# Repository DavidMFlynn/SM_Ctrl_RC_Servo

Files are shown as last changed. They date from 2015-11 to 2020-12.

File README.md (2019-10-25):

# SM_Ctrl_RC_Servo
Model railroad switch machine controller.
Uses a small (SG90) R/C Servo as a switch machine.
Built for the Highland Pacific, 854 East Broadway, San Gabriel, CA 91776, USA
GPL 3+
If you find it useful let me know dflynn at oxfordvue.com
The G2R Rev B may be the final version. A remote config connector and a big capacitor were added.
My faverite servo is the hobbyking HX5010 it's inexpensive and well behaved.

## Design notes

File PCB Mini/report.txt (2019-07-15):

Info: Backing up file “/Projects/SM_Ctrl_RC_Servo/PCB Mini/sym-lib-table” to file “/Projects/SM_Ctrl_RC_Servo/PCB Mini/rescue-backup/sym-lib-table-2019-07-13-21-21-59”.
Info: Backing up file “/Projects/SM_Ctrl_RC_Servo/PCB Mini/RCSMCtrl.sch” to file “/Projects/SM_Ctrl_RC_Servo/PCB Mini/rescue-backup/RCSMCtrl-2019-07-13-21-21-59.sch”.
Info: Backing up file “/Projects/SM_Ctrl_RC_Servo/PCB Mini/RCSMCtrl.pro” to file “/Projects/SM_Ctrl_RC_Servo/PCB Mini/rescue-backup/RCSMCtrl-2019-07-13-21-21-59.pro”.
Info: Backing up file “/Projects/SM_Ctrl_RC_Servo/PCB Mini/RCSMCtrl-cache.lib” to file “/Projects/SM_Ctrl_RC_Servo/PCB Mini/rescue-backup/RCSMCtrl-cache-2019-07-13-21-21-59.lib”.
Info: Backing up file “/Projects/SM_Ctrl_RC_Servo/PCB Mini/RCSMCtrl-rescue.lib” to file “/Projects/SM_Ctrl_RC_Servo/PCB Mini/rescue-backup/RCSMCtrl-rescue-2019-07-13-21-21-59.lib”.
Info: Backing up file “/Projects/SM_Ctrl_RC_Servo/PCB Mini/RCSMCtrl-rescue.dcm” to file “/Projects/SM_Ctrl_RC_Servo/PCB Mini/rescue-backup/RCSMCtrl-rescue-2019-07-13-21-21-59.dcm”.
Info: Adding library “RCSMCtrl-rescue”, file “${KIPRJMOD}/RCSMCtrl-rescue.lib” to project symbol library table.
Symbol “PIC12(L)F1822-I_P” mapped to symbol library “RCSMCtrl-rescue”.
Symbol “D” mapped to symbol library “Device”.
Symbol “CP1_Small” mapped to symbol library “Device”.
Symbol “C_Small” mapped to symbol library “Device”.
Symbol “C_Small” mapped to symbol library “Device”.
Symbol “LM7805CT” mapped to symbol library “RCSMCtrl-rescue”.
Symbol “CONN_01X15” mapped to symbol library “RCSMCtrl-rescue”.
Symbol “+5V” mapped to symbol library “power”.
Symbol “GND” mapped to symbol library “power”.
Symbol “+24V” mapped to symbol library “power”.
Symbol “GND” mapped to symbol library “power”.
Symbol “CONN_01X03” mapped to symbol library “RCSMCtrl-rescue”.
Symbol “+5V” mapped to symbol library “power”.
Symbol “GND” mapped to symbol library “power”.
Symbol “R” mapped to symbol library “Device”.
Symbol “+5V” mapped to symbol library “power”.
Symbol “GND” mapped to symbol library “power”.
Symbol “R” mapped to symbol library “Device”.
Symbol “D” mapped to symbol library “Device”.
Symbol “R” mapped to symbol library “Device”.
Symbol “R” mapped to symbol library “Device”.
Symbol “C_Small” mapped to symbol library “Device”.
Symbol “Q_NPN_EBC” mapped to symbol library “Device”.
Symbol “Q_PNP_EBC” mapped to symbol library “Device”.
Symbol “R” mapped to symbol library “Device”.
Symbol “GND” mapped to symbol library “power”.
Symbol “+5V” mapped to symbol library “power”.
Symbol “GND” mapped to symbol library “power”.
Symbol “SW_PUSH” mapped to symbol library “RCSMCtrl-rescue”.
Symbol “SW_PUSH” mapped to symbol library “RCSMCtrl-rescue”.
Symbol “LED” mapped to symbol library “Device”.
Symbol “LED” mapped to symbol library “Device”.
Symbol “+5V” mapped to symbol library “power”.
Symbol “R” mapped to symbol library “Device”.
Symbol “R” mapped to symbol library “Device”.
Symbol “R” mapped to symbol library “Device”.
Symbol “R” mapped to symbol library “Device”.
Symbol “GND” mapped to symbol library “power”.
Symbol “D” mapped to symbol library “Device”.
Symbol “D” mapped to symbol library “Device”.
Symbol “GND” mapped to symbol library “power”.
Symbol “+24V” mapped to symbol library “power”.
Symbol “R” mapped to symbol library “Device”.
Symbol “R” mapped to symbol library “Device”.
Symbol “Q_NPN_EBC” mapped to symbol library “Device”.
Symbol “D” mapped to symbol library “Device”.
Symbol “D” mapped to symbol library “Device”.
Symbol “GND” mapped to symbol library “power”.
Symbol “+24V” mapped to symbol library “power”.
Symbol “R” mapped to symbol library “Device”.
Symbol “R” mapped to symbol library “Device”.
Symbol “IM00” mapped to symbol library “RCSMCtrl-rescue”.
Symbol “IM00” mapped to symbol library “RCSMCtrl-rescue”.
Info: Symbol library table mapping complete!

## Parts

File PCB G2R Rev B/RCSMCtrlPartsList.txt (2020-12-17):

R/C Servo Sitch Machine Controller Parts List
=========================================================
P1	Wires 15 x 10" 20AWG
P2	Connector 3 pin .1cl

K1,K2	Relay G2R 24VDC DPDT (1 or 2)

U1	LM7805 DPAK
IC1	Socket 8 pin dip (optional)
IC1	PIC12F1822

Q1,Q3	2N7000 40V N-Ch FET TO-92 (2)
Q2	2N3906 40V PNP TO-92

D1,D2,D3,D4,D7,D8	Diode 200V Fast SMA (6)
D5,D6	LED 1206 (2)
SW1,SW1	Switch SMT SPST

C1,C3,C4,C6	Cap 0.1uf 0805 (3)
C2	Cap 33uf 50v
C5                     Cap 220uf 16v

R1,R5,R6,R7,R9,R12	Res 47KΩ 0805 (6)
R2,R3,R8,R10,R13	Res 1KΩ 0805 (5)
R4	Res 10KΩ 0805
R11	Res 220Ω 0805

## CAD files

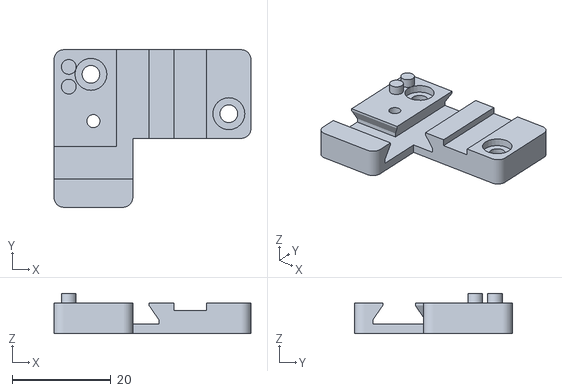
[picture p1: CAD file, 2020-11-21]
MountingBox/AtlasTurnout STL/RAMountingBlock.stl
40.0 x 32.0 x 8.15

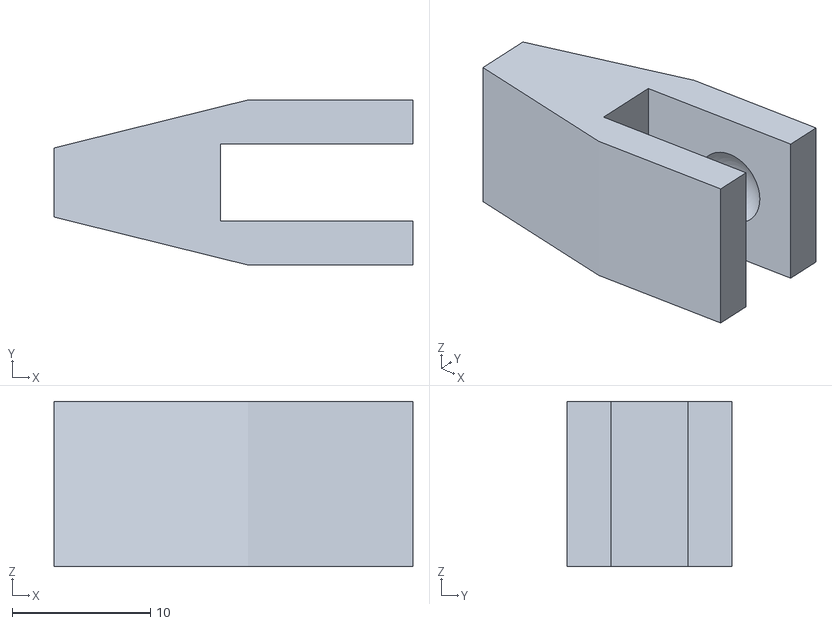
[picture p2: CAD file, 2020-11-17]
MountingBox/STL/RodConnector.stl
26.0 x 11.9 x 11.9

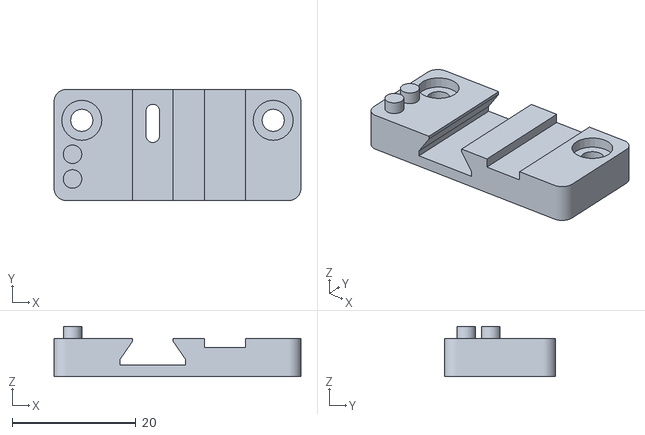
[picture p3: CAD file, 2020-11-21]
MountingBox/AtlasTurnout STL/MountingBlockMir.stl
40.0 x 18.0 x 8.15

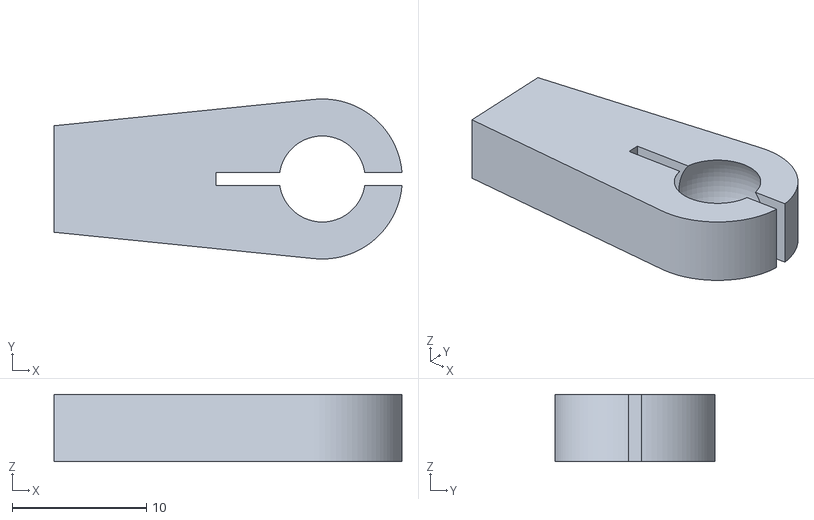
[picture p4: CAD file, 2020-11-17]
MountingBox/STL/RodEnd.stl
25.9 x 11.9 x 5.00

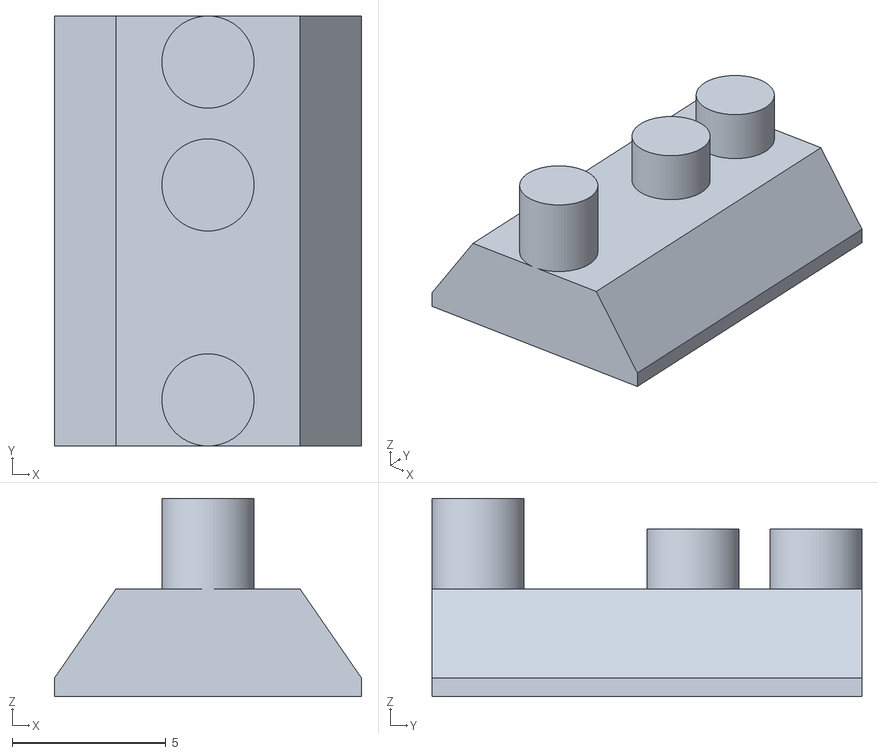
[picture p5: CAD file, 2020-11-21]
MountingBox/AtlasTurnout STL/RASlider.stl
10.0 x 14.0 x 6.45

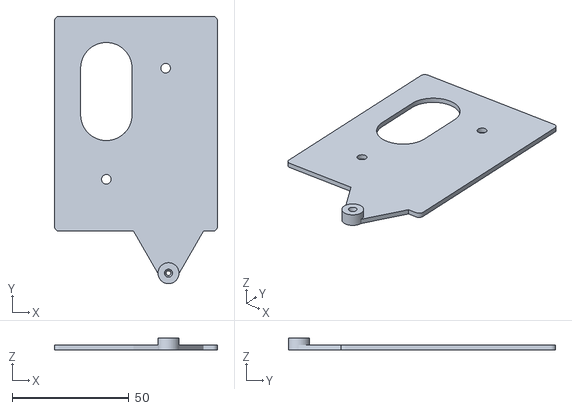
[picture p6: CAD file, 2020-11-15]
MountingBox/STL/PivotBaseR.stl
69.8 x 114.6 x 5.00

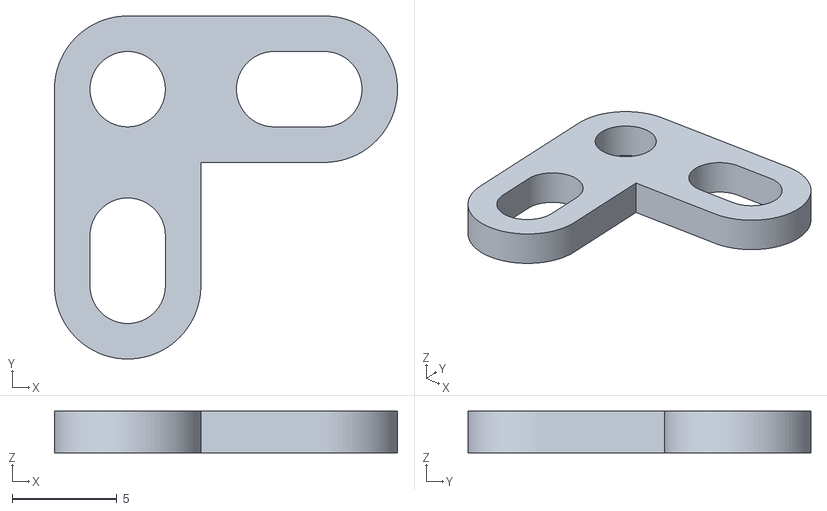
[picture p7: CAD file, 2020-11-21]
MountingBox/AtlasTurnout STL/RAPivot.stl
16.4 x 16.4 x 2.00

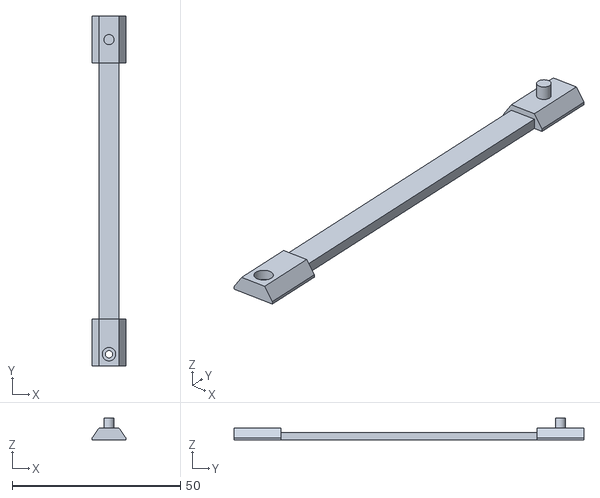
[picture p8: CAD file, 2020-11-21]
MountingBox/AtlasTurnout STL/RAExtension90.stl
10.0 x 104.0 x 6.45

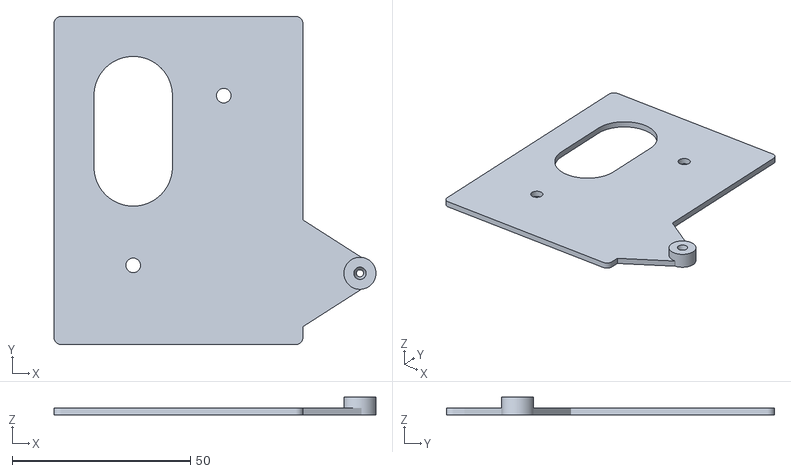
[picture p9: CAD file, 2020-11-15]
MountingBox/STL/PivotBaseRS.stl
90.3 x 92.1 x 5.00

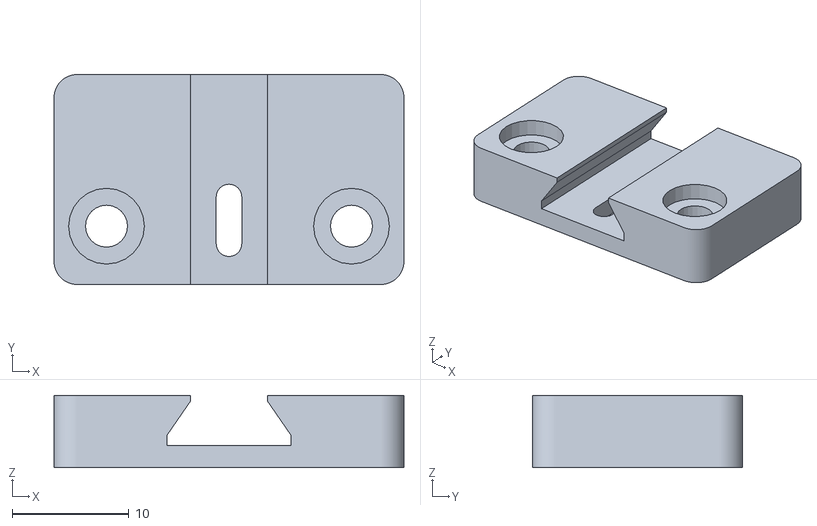
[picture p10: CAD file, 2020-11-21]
MountingBox/AtlasTurnout STL/ExtenderMount.stl
30.0 x 18.0 x 6.20

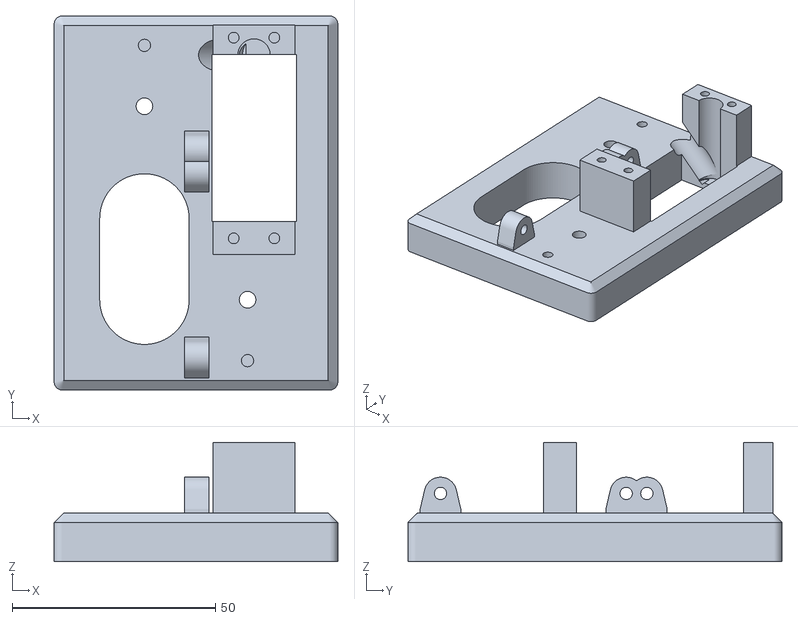
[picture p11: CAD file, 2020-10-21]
MountingBox/STL/ServoSMBlockHX5010.stl
69.8 x 92.1 x 29.3

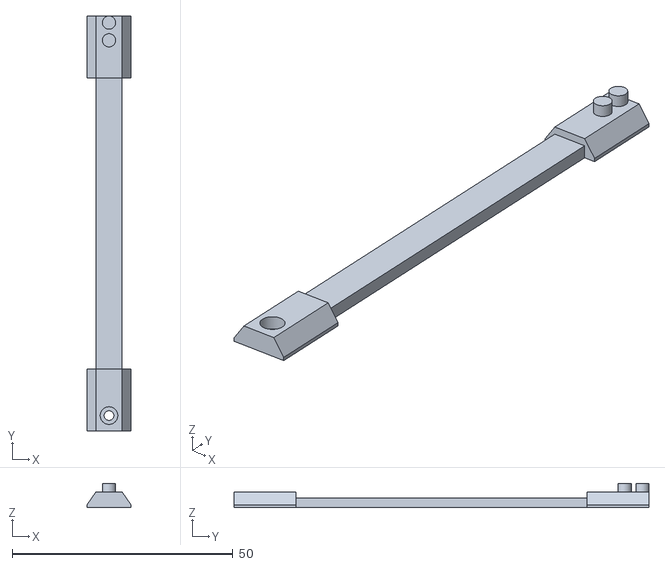
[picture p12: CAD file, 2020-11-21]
MountingBox/AtlasTurnout STL/ExtendedSlider80.stl
10.0 x 94.0 x 5.45

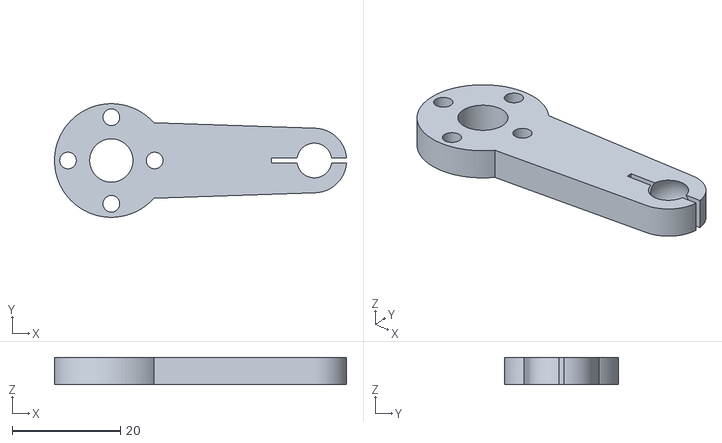
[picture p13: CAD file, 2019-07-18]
MountingBox/STL/ServoArmMG996R.stl
53.9 x 21.0 x 5.00

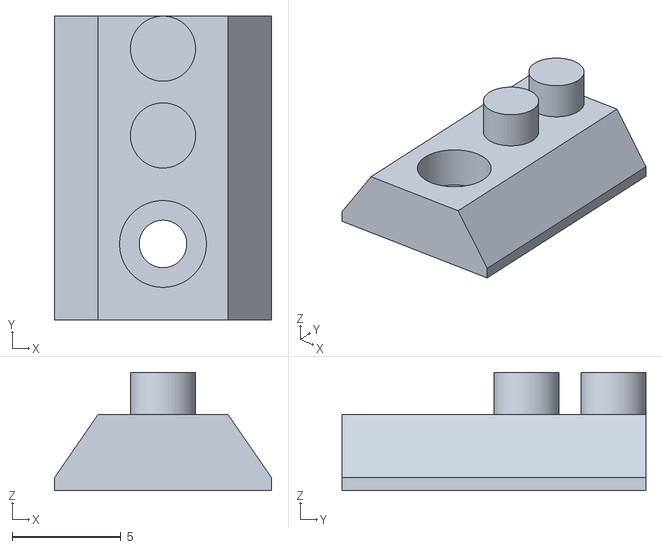
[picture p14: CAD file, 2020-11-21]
MountingBox/AtlasTurnout STL/Slider.stl
10.0 x 14.0 x 5.45

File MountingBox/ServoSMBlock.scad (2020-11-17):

// *************************************************
// Standard Servo Switch Machine Block & Adaptor
// by Dave Flynn
// Filename:ServoSMBlock.scad
// Created: 8/18/2018
// Revision: 1.2 11/16/2020
// Units: mm
// **************************************************
//  ***** History ******
// 1.2 11/16/2020 Added extension arm parts
// 1.1 10/26/2020 Added PivotBase
// 1.0b1 8/6/2019 Added #6 screw hole for wire strain relief.
// 1.0a2 8/4/2019 Common mounting for PCB.
// 1.0a1 7/17/2019 RC1, Servo and PCB mount, Ball servo horn.
// 1.0d1 8/18/2018 First rev'd version
//
// **************************************************
//  ***** for STL output *****
// Arm(L=37.5);
//
// RodEnd(L=20); // part of extension arm
// rotate([90,0,0]) RodConnector(L=20); // part of extension arm
//
// SMBlock(PCBMount="Both");
// mirror([1,0,0]) SMBlock(PCBMount="Both"); // Left side mount
// SMBlock(PCBMount="G2RrA");
// mirror([1,0,0]) SMBlock(PCBMount="G2RrA"); // Left side mount
//
// rotate([180,0,0]) PivotBase(); // for right mount
// rotate([180,0,0]) mirror([1,0,0]) PivotBase(); // for left mount
// rotate([180,0,0]) PivotBaseSide(); // for right side mount
// rotate([180,0,0]) mirror([1,0,0]) PivotBaseSide(); // for left side mount
//
// **************************************************


include<CommonStuffSAEmm.scad>
include<LD-20MGServoLib.scad>

$fn=90;
Overlap=0.05;
IDXtra=0.2;

module RodConnector(L=20){
	Ball_d=5/16*25.4;
	Arm_h=5;
	
	difference(){
		hull(){
			translate([0,-Ball_d/2-2,-Arm_h/2]) cube([0.1,Ball_d+4,Arm_h]);
			
			translate([L,0,0]) //cylinder(d=Ball_d+4,h=Ball_d+4,center=true);
			cube([Ball_d+4,Ball_d+4,Ball_d+4],center=true);
		} // hull
		
		
		//Mounting Rod
		translate([0,0,0]) rotate([0,-90,0]) Bolt6Hole(depth=10);
		
		// the ball
		translate([L,0,0]) sphere(d=Ball_d+IDXtra,$fn=60);
		translate([L,0,0]) cube([Ball_d+8,Ball_d+7,Arm_h+IDXtra*3],center=true); //cylinder(d=Ball_d+7,h=Arm_h+IDXtra*3,center=true);
		
		
	} // difference
} // RodConnector

//RodConnector();

module RodEnd(L=20){
	Ball_d=5/16*25.4;
	Arm_h=5;
	
	difference(){
			
		hull(){
			translate([0,-Ball_d/2,0]) cube([0.1,Ball_d,Arm_h]);
			translate([L,0,0]) cylinder(d=Ball_d+4,h=Arm_h);
		} // hull
			
		//Mounting Rod
		translate([0,0,Arm_h/2]) rotate([0,-90,0]) Bolt6Hole(depth=10);
		// the ball
		translate([L,0,Arm_h/2]) sphere(d=Ball_d+IDXtra,$fn=60);
		//translate([L,0,-Overlap]) cylinder(d=Ball_d*0.707,h=Arm_h+Overlap*2);
		
		// slot
		translate([L-Ball_d,-0.5,-Overlap]) cube([Ball_d*2+Overlap,1,Arm_h+Overlap*2]);
		
	} // diff
	
} // RodEnd

//RodEnd();

module Arm(L=37.5){
	// Arm for MG996R servo
	//Ball_d=3/8*25.4;
	Ball_d=5/16*25.4;
	Arm_h=5;
	S_Wheel_d=21;
	
	module ArmBall(){
		Wire_d=0.055*25.4;
		
		difference(){
			sphere(d=Ball_d,$fn=30);
			translate([0,0,-Ball_d/2-Overlap]) cylinder(d=Wire_d+IDXtra,h=Ball_d+Overlap*2);
		} // diff
	} // ArmBall

	//ArmBall();
	
	difference(){
		union(){
			cylinder(d=S_Wheel_d,h=Arm_h);
			
			hull(){
				cylinder(d=(S_Wheel_d+Ball_d)/2,h=Arm_h);
				
				translate([L,0,0]) cylinder(d=Ball_d+4,h=Arm_h);
			} // hull
			
		} // union
		
		// the ball
		translate([L,0,Arm_h/2]) sphere(d=Ball_d+IDXtra,$fn=60);
		translate([L,0,-Overlap]) cylinder(d=Ball_d*0.707,h=Arm_h+Overlap*2);
		
		// slot
		translate([L-Ball_d,-0.5,-Overlap]) cube([Ball_d*2+Overlap,1,Arm_h+Overlap*2]);
		
		// screw access
		translate([0,0,-Overlap]) cylinder(d=8,h=Arm_h+Overlap*2);
		
		// Mounting screws
		for (j=[0:3]) rotate([0,0,90*j]) translate([8,0,Arm_h]) Bolt2ClearHole();
	} // diff
	
	
} // Arm

//Arm(L=37.5);

module RoundRect(X=10,Y=10,Z=2,R=1){
	hull(){
	translate([-X/2+R,-Y/2+R,0]) cylinder(r=R,h=Z);
	translate([X/2-R,-Y/2+R,0]) cylinder(r=R,h=Z);
	translate([-X/2+R,Y/2-R,0]) cylinder(r=R,h=Z);
	translate([X/2-R,Y/2-R,0]) cylinder(r=R,h=Z);
	}
} // RoundRect

module SMBlock(PCBMount="Both"){
	// or "G2RrA" or "G2RMini" or "Both"
	
	Block_x=2.75*25.4;
	Block_y=3.625*25.4;
	Block_z=12; // 0.75*25.4;
	BlockChamfer=0.094*25.4;
	
	Shaft_x=0.5625*25.4;
	Shaft_y=1.0*25.4;
	Shaft_z=50; // 2.5*25.4;
	Servo_Shaft_Offset=9.85;
	Servo_TopOfWheel=20.6;
	Servo_y=54.5;
	Servo_Body_l=40.5;
	Servo_h1=19.3; // bottom of servo to bottom of mount
	Servo_w=20.2;
	
	MH_x=1*25.4;
	MH_y=1.875*25.4;
	
	// G2R Rev A
	PCBG2RrA_X=2.3*25.4;
	PCBG2RrA_Y=2.10*25.4;
	PCBG2RrA_BC_X=1.80*25.4;
	PCBG2RrA_Bolt_Y=0.15*25.4;
	PCBG3RrA_Loc_Y=-Block_y/2+8;

	
	// G2R Mini PCB
	PCB_X=2.3*25.4;
	PCB_Y=1.85*25.4;
	PCB_BC_X=2.0*25.4;
	PCB_Bolt_Y=0.15*25.4;
	PCB_Loc_Y=-Block_y/2+8;
	
	difference(){
		union(){
			hull(){
				//translate([0,0,(Block_z-BlockChamfer)/2]) cube([Block_x,Block_y,Block_z-BlockChamfer],center=true);
				RoundRect(X=Block_x,Y=Block_y,Z=Block_z-BlockChamfer,R=2);
				translate([0,0,Block_z/2]) cube([Block_x-BlockChamfer*2,Block_y-BlockChamfer*2,Block_z],center=true);
			} // hull
			
			// Servo mounts
			translate([Shaft_x-(Servo_w/2-Overlap),Shaft_y-Servo_Shaft_Offset-(Servo_y/2+1),0]) 
				cube([Servo_w-Overlap*2,Servo_y+2,Servo_h1+10]);
		} // union
		
		// mounting holes
		translate([-MH_x/2,MH_y/2,Block_z]) Bolt6ClearHole(depth=Block_z);
		translate([MH_x/2,-MH_y/2,Block_z]) Bolt6ClearHole(depth=Block_z);
		
		// ty-wrap screw
		translate([-MH_x/2,MH_y/2+15,Block_z]) Bolt6Hole(depth=Block_z-1);
		translate([MH_x/2,-MH_y/2-15,Block_z]) Bolt6Hole(depth=Block_z-1);
		
		//wire path
		translate([Shaft_x,Shaft_y+11,2]) cylinder(d=8,h=30);
		translate([Shaft_x,Shaft_y+11,4]) rotate([0,-45,0]) cylinder(d=8,h=30);
		
		// Servo
		translate([Shaft_x,Shaft_y,Shaft_z-Servo_TopOfWheel]) rotate([0,0,90]) Servo_HX5010(BottomMount=false,TopAccess=false,Xtra_w=0.6, Xtra_h=5);
		//Servo_LD20MG(BottomMount=false,TopAccess=false);
		// remove servo bottom
		//translate([Shaft_x-10.25,Shaft_y-20-10,-Overlap]) cube([20.5,40.5,3]);
	
		// Remove extra
		translate([-MH_x/2,-MH_y/2,-Overlap])hull(){
			cylinder(d=22,h=Block_z+Overlap*2);
			translate([0,20,0]) cylinder(d=22,h=Block_z+Overlap*2);
		}
	
	} // diff
	
	//PCB mount for RC servo controller
	
	translate([1,0,Block_z-Overlap])
		difference(){
			union(){
				if (PCBMount=="G2RMini" || PCBMount=="Both"){
				translate([-PCB_Bolt_Y,PCB_Loc_Y,0])  hull(){
					translate([0,0,PCB_Bolt_Y+1]) rotate([0,90,0]) cylinder(d=8,h=6);
					translate([0,-5,0]) cube([6,10,1]);}
					
				translate([-PCB_Bolt_Y,PCB_Loc_Y+PCB_BC_X,0])  hull(){
					translate([0,0,PCB_Bolt_Y+1]) rotate([0,90,0]) cylinder(d=8,h=6);
					translate([0,-5,0]) cube([6,10,1]);}
				}
				
				if (PCBMount=="G2RrA" || PCBMount=="Both"){
					translate([-PCBG2RrA_Bolt_Y,PCBG3RrA_Loc_Y,0])  hull(){
						translate([0,0,PCBG2RrA_Bolt_Y+1]) rotate([0,90,0]) cylinder(d=8,h=6);
						translate([0,-5,0]) cube([6,10,1]);}
					
					translate([-PCBG2RrA_Bolt_Y,PCBG3RrA_Loc_Y+PCBG2RrA_BC_X,0])  hull(){
						translate([0,0,PCBG2RrA_Bolt_Y+1]) rotate([0,90,0]) cylinder(d=8,h=6);
						translate([0,-5,0]) cube([6,10,1]);}
				}
				
			} // union
		if (PCBMount=="G2RMini" || PCBMount=="Both"){
			translate([-PCB_Bolt_Y,PCB_Loc_Y,PCB_Bolt_Y+1]) rotate([0,-90,0])Bolt6Hole();
			translate([-PCB_Bolt_Y,PCB_Loc_Y+PCB_BC_X,PCB_Bolt_Y+1]) rotate([0,-90,0])Bolt6Hole();
		}
			
		if (PCBMount=="G2RrA" || PCBMount=="Both"){
			translate([-PCBG2RrA_Bolt_Y,PCBG3RrA_Loc_Y,PCBG2RrA_Bolt_Y+1]) rotate([0,-90,0]) Bolt6Hole();
			translate([-PCBG2RrA_Bolt_Y,PCBG3RrA_Loc_Y+PCBG2RrA_BC_X,PCBG2RrA_Bolt_Y+1]) rotate([0,-90,0]) Bolt6Hole();
		}
		} // diff
	
		/*
	if (PCBMount=="G2RrA" || PCBMount=="Both")
	translate([1,PCBG3RrA_Loc_Y,Block_z-Overlap]){
		difference(){
			union(){
				translate([-PCBG2RrA_Bolt_Y,-PCBG2RrA_BC_X/2,0])  hull(){
					translate([0,0,PCBG2RrA_Bolt_Y+1]) rotate([0,90,0]) cylinder(d=8,h=6);
					translate([0,-5,0]) cube([6,10,1]);}
					
				translate([-PCBG2RrA_Bolt_Y,PCBG2RrA_BC_X/2,0])  hull(){
					translate([0,0,PCBG2RrA_Bolt_Y+1]) rotate([0,90,0]) cylinder(d=8,h=6);
					translate([0,-5,0]) cube([6,10,1]);}
			} // union
		
			translate([-PCBG2RrA_Bolt_Y,-PCBG2RrA_BC_X/2,PCBG2RrA_Bolt_Y+1]) rotate([0,-90,0]) Bolt6Hole();
			translate([-PCBG2RrA_Bolt_Y,PCBG2RrA_BC_X/2,PCBG2RrA_Bolt_Y+1]) rotate([0,-90,0]) Bolt6Hole();}
		} // diff
		/**/
	// PCB G2R Mini
	//translate([-3,PCB_Loc_Y,0])
	//translate([0,-PCB_X/2,Block_z]) color("Red") rotate([0,-90,0]) cube([PCB_Y,PCB_X,1.5]);
	
		// PCB G2R Rev A
	//translate([-4.5,PCBG3RrA_Loc_Y,0])
	//translate([0,-PCBG2RrA_X/2,Block_z]) color("Red") rotate([0,-90,0]) cube([PCBG2RrA_Y,PCBG2RrA_X,1.5]);

} // SMBlock

//SMBlock();
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

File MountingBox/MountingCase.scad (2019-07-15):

// ******************************************
// R/C Servo Switch Machine Controller Case
// by David Flynn
// Created: 8/4/2017
// Revision: 1.3 5/15/2019
// Units: mm
// ******************************************
// History
// 1.3 5/15/2019 Added Vertical Servo Mounting
// 1.2 5/14/2019 Converted to mm
// 1.1 9/13/2017 Deeper, rounder, bigger text.
// 1.0 8/4/2017
// ******************************************
// for STL output
//rotate([180,0,0])CaseTop(OneRly=false);
//rotate([180,0,0])CaseTop(OneRly=true);
//CaseBase();
//SG90Mount();
//
//  *** Vertical Servo Mount ***
//VMountDrillGuide();
//VMountServo();
//rotate([180,0,0]) VMountCtoS();
//*******************************************
include <CommonStuffSAEmm.scad>

$fn=90;
Overlap=0.05;
IDXtra=0.2;

CaseWall_t=2;
PCB_OA_z=0.556*25.4; // to C2, 0.393 to IC1, not counting the relays
Base_h=0.4*25.4;

PCB_x=2.1*25.4;
PCB_y=2.3*25.4;
PCB_Bolt_x=1.925*25.4;
PCB_Bolt1_y=0.25*25.4;
PCB_Bolt2_y=2.05*25.4;
PCB_t=0.062*25.4+0.03*25.4; // 0.03 is gap
PCB_Bot=CaseWall_t+0.05*25.4;
Top_h=PCB_OA_z-Base_h+PCB_Bot+CaseWall_t;   //0.2;

MountingHoleSpacing=3*25.4;
PCB_Inset=0.05*25.4;

	Case_x=PCB_x+PCB_Inset*2+CaseWall_t*2;
	Case_y=PCB_y+PCB_Inset*2+CaseWall_t*2;

module RoundRect(X=10,Y=10,H=10,R=1){
	translate([0,0,-H/2])hull(){
		translate([-X/2+R,-Y/2+R,0])cylinder(r=R,h=H);
		translate([X/2-R,-Y/2+R,0])cylinder(r=R,h=H);
		translate([-X/2+R,Y/2-R,0])cylinder(r=R,h=H);
		translate([X/2-R,Y/2-R,0])cylinder(r=R,h=H);
	} // hull
} // RoundRect

//RoundRect();

module CaseBase(){
	difference(){
		union(){
			translate([0,0,Base_h/2])
				RoundRect(X=Case_x,Y=Case_y,H=Base_h,R=1);
			
			// mounting tabs
			hull(){
				translate([0,-MountingHoleSpacing/2,0]) cylinder(d=12.7,h=3);
				translate([0,MountingHoleSpacing/2,0]) cylinder(d=12.7,h=3);
			} // hull
			
			
		} // union
		
		translate([0,0,Base_h/2+CaseWall_t])
			RoundRect(X=PCB_x+PCB_Inset*2,Y=PCB_y+PCB_Inset*2,H=Base_h,R=1);
		
		translate([0,-MountingHoleSpacing/2,3]) Bolt6ClearHole();
		translate([0,MountingHoleSpacing/2,3]) Bolt6ClearHole();
		// PCB mounting screws
		translate([-PCB_x/2+PCB_Bolt_x,-PCB_y/2,PCB_Bot]){
				translate([0,PCB_Bolt1_y,0]) Bolt4Hole();
				translate([0,PCB_Bolt2_y,0]) Bolt4Hole();
			}
			
		// case screws
		translate([-Case_x/2+5,-Case_y/2-CaseWall_t,Base_h/2]) rotate([90,0,0]) Bolt4Hole();
		mirror([0,1,0])
		translate([-Case_x/2+5,-Case_y/2-CaseWall_t,Base_h/2]) rotate([90,0,0]) Bolt4Hole();
	} // diff
	// PCB mounting screws
	difference(){
	translate([-PCB_x/2+PCB_Bolt_x,-PCB_y/2,0]){
				translate([0,PCB_Bolt1_y,0]) cylinder(d=8,h=PCB_Bot);
				translate([0,PCB_Bolt2_y,0]) cylinder(d=8,h=PCB_Bot);
			}
			translate([-PCB_x/2+PCB_Bolt_x,-PCB_y/2,PCB_Bot]){
				translate([0,PCB_Bolt1_y,0]) Bolt4Hole();
				translate([0,PCB_Bolt2_y,0]) Bolt4Hole();
			}
		} // diff
} // CaseBase

//translate([0,0,-Base_h-Overlap])CaseBase();

W1_y=2.2*25.4;
W2_y=0.1*25.4;
LED_x=1.6*25.4;
LED1_y=1.475*25.4;
LED2_y=1.15*25.4;
SW_x=1.9*25.4;
SW1_y=1.525*25.4;
SW2_y=1.075*25.4;
Rly_x=0.3*25.4;
Rly_y=0.05*25.4;
Rly_w=1.2*25.4;
Rly_h=1.1*25.4;
P2_x=1.375*25.4;
P2_y=2.075*25.4;
P2_w=0.350*25.4;
P2_h=0.150*25.4;

module CaseTop(OneRly=false){
	difference(){
		translate([0,0,Top_h/2])
			RoundRect(X=Case_x,Y=Case_y,H=Top_h,R=1);
		
		translate([0,0,Top_h/2-CaseWall_t])
			RoundRect(X=PCB_x+PCB_Inset*2,Y=PCB_y+PCB_Inset*2,H=Top_h,R=1);
		
		// PCB mounting screws
		translate([-PCB_x/2+PCB_Bolt_x,-PCB_y/2,Top_h]){
				translate([0,PCB_Bolt1_y,0]) Bolt4HeadHole();
				translate([0,PCB_Bolt2_y,0]) Bolt4HeadHole();
		}
		// Relays
		if (OneRly==true){
			translate([-PCB_x/2+Rly_x,-PCB_y/2+Rly_y+Rly_h/2,0]) cube([Rly_w,Rly_h/2,Top_h+Overlap]);
		}else{
		translate([-PCB_x/2+Rly_x,-PCB_y/2+Rly_y,0]) cube([Rly_w,Rly_h,Top_h+Overlap]);}
		
		// Servo connector
		translate([-PCB_x/2+P2_x,-PCB_y/2+P2_y,0]) cube([P2_w,P2_h,Top_h+Overlap]);
		
		// wires
		translate([-Case_x/2-Overlap,-PCB_y/2+W2_y-1,-Overlap])cube([CaseWall_t+Overlap*2,W1_y-W2_y+3,3]);
		// LEDs
		translate([-PCB_x/2+LED_x,-PCB_y/2,0]){
			translate([0,LED1_y,0])	cylinder(d=3,h=Top_h+Overlap);
			translate([0,LED2_y,0])	cylinder(d=3,h=Top_h+Overlap);}
		// Switches
		translate([-PCB_x/2+SW_x,-PCB_y/2,0]){
			translate([0,SW1_y,0])	cylinder(d=3,h=Top_h+Overlap);
			translate([0,SW2_y,0])	cylinder(d=3,h=Top_h+Overlap);}
			
		// Text
			TestDepth=0.0236*25.4;
		translate([-PCB_x/2,-PCB_y/2,Top_h-TestDepth]){
			translate([LED_x-2,LED1_y+3,0]) linear_extrude(height=TestDepth) text("N",5);
			translate([LED_x-2,LED2_y-8,0]) linear_extrude(height=TestDepth) text("R",5);
			translate([SW_x-2,SW1_y+3,0]) linear_extrude(height=TestDepth) text("+",6);
			translate([SW_x-2,SW2_y-3-1,0]) linear_extrude(height=TestDepth) text("_",6);
			translate([P2_x-5,P2_y,0]) linear_extrude(height=TestDepth) text("S",5);
			translate([P2_x+2.5,P2_y+4,0]) linear_extrude(height=TestDepth) text("+ -",5);
			translate([0.00,PCB_y-6,0]) linear_extrude(height=TestDepth) text("R/C",6);
			translate([0.00,PCB_y-13,0]) linear_extrude(height=TestDepth) text("Servo SM",6);
			translate([5,PCB_y-60,0]) rotate([0,0,90]) linear_extrude(height=TestDepth) text("DMFE 2019",6);
			
		}
	} // diff
	
	// PCB mounting screws
	Post_l=Base_h-PCB_Bot-PCB_t+Top_h-Overlap;
	difference(){
			translate([-PCB_x/2+PCB_Bolt_x,-PCB_y/2,-Base_h+PCB_Bot+PCB_t]){
				translate([0,PCB_Bolt1_y,0]) cylinder(d=8,h=Post_l);
				translate([0,PCB_Bolt2_y,0]) cylinder(d=8,h=Post_l);
			}
			translate([-PCB_x/2+PCB_Bolt_x,-PCB_y/2,Top_h]){
				translate([0,PCB_Bolt1_y,0]) Bolt4HeadHole(depth=Top_h+Base_h);
				translate([0,PCB_Bolt2_y,0]) Bolt4HeadHole(depth=Top_h+Base_h);
			}
		} // diff
		
	// case screws
	difference(){
		union(){
			translate([-Case_x/2,-Case_y/2-CaseWall_t/2,0]) cube([11,CaseWall_t,Top_h]);
			translate([-Case_x/2,-Case_y/2-CaseWall_t-IDXtra,-Base_h]) cube([11,CaseWall_t,Base_h+Top_h]);
		} // union
			
		translate([-Case_x/2+5,-Case_y/2-CaseWall_t-IDXtra,-Base_h/2]) rotate([90,0,0]) Bolt4ClearHole();
	} // diff
	mirror([0,1,0])
	difference(){
		union(){
			translate([-Case_x/2,-Case_y/2-CaseWall_t/2,0]) cube([11,CaseWall_t,Top_h]);
			translate([-Case_x/2,-Case_y/2-CaseWall_t-IDXtra,-Base_h]) cube([11,CaseWall_t,Base_h+Top_h]);
		} // union
		
		translate([-Case_x/2+4,-Case_y/2-CaseWall_t-IDXtra,-Base_h/2]) rotate([90,0,0]) Bolt4ClearHole();
	} // diff
} // CaseTop

//CaseTop(OneRly=true);

SG90_t=0.5*25.4;
SG90Ear_w=0.190*25.4;
SG90Ear_t=0.100*25.4;
SG90Body_w=0.893*25.4;
SG90Bot_h=0.652*25.4;
SG90Top_h=0.266*25.4;
SG90DriveBoss_d=0.454*25.4;
SG90DriveBoss_h=0.460*25.4;
SG90Drive_h=0.626*25.4;
SG90HoleOffset=0.100*25.4;
	SG90Mount_w=0.375*25.4;
	SG90Mount_t=0.250*25.4;

module SG90Servo(){
	translate([-SG90Body_w/2,0,-SG90_t/2])cube([SG90Body_w,SG90Bot_h,SG90_t]);
	difference(){
		translate([-SG90Body_w/2-SG90Ear_w,-SG90Ear_t,-SG90_t/2]) cube([SG90Body_w+SG90Ear_w*2,SG90Ear_t,SG90_t]);
		translate([-SG90Body_w/2-SG90HoleOffset,-SG90Ear_t,0]) rotate([90,0,0])Bolt2ClearHole();
		translate([SG90Body_w/2+SG90HoleOffset,-SG90Ear_t,0]) rotate([90,0,0])Bolt2ClearHole();
	} // diff
	translate([-SG90Body_w/2,-SG90Top_h,-SG90_t/2])cube([SG90Body_w,SG90Top_h,SG90_t]);
	translate([-SG90Body_w/2+SG90DriveBoss_d/2,-SG90DriveBoss_h,0])rotate([-90,0,0])cylinder(d=SG90DriveBoss_d,h=SG90DriveBoss_h);
	translate([-SG90Body_w/2+SG90DriveBoss_d/2,-SG90Drive_h,0])rotate([-90,0,0])cylinder(d=7,h=SG90Drive_h);
	translate([-SG90Body_w/2+SG90DriveBoss_d/2,-SG90Drive_h,0])rotate([-90,0,0])cylinder(d=19,h=1);
	
} // SG90Servo

//color("Red")SG90Servo();

ServoWheelOffset=5.5;
WingCL=15;

module VMountDrillGuide(){
	VMS_h=3;
	
	difference(){
		union(){
			hull(){
				translate([ServoWheelOffset,WingCL,0]) cylinder(d=10,h=VMS_h);
				translate([ServoWheelOffset,-WingCL,0]) cylinder(d=10,h=VMS_h);
				cylinder(d=10,h=VMS_h);
			}
		 // handlle
			hull(){
				translate([20,0,0]) cylinder(d=3,h=15);
			translate([5.5,0,0]) cylinder(d=3,h=15);
			}
	}
		translate([ServoWheelOffset,WingCL,0]) rotate([180,0,0]) Bolt6ClearHole();
		translate([ServoWheelOffset,-WingCL,0]) rotate([180,0,0]) Bolt6ClearHole();
		rotate([180,0,0]) Bolt6ClearHole();
	}
} // VMountDrillGuide

//VMountDrillGuide();
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

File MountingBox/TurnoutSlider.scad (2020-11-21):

// ****************************************
// Turnout slider
// Filename: TurnoutSlider.scad
// by Dave Flynn
// Created: 10/20/2020
// Revision: 1.2.2 11/20/2020
// Units: mm
// ****************************************
//  ***** History *****
//
// 1.2.2 11/20/2020 Code clean up.
// 1.2.1 11/20/2020 Adjusted RA clearances, added ShowRAExt();
// 1.2   11/19/2020 Added Right Angle Extension
// 1.1   11/17/2020 Added ExtendedSlider and mount
// 1.0   10/21/2020 Turnout lock.
// 0.9   10/20/2020 First code.
//
// ****************************************
//  ***** for STL output *****
//
// MountingBlock(HasLock=false);
// mirror([0,1,0]) MountingBlock(HasLock=false);
// MountingBlock(HasLock=true); // for #6 left
// mirror([0,1,0]) MountingBlock(HasLock=true); // for #6 right
//
// Slider();
// ExtendedSlider(L=80);
// ExtenderMount(); // used with ExtendedSlider
//
// *** Right Angle Extension Parts ***
// RAMountingBlock();
// RASlider();
// RAPivot();
// RAExtension(L=90);
// ExtenderMount();
//
// ****************************************
//  ***** for Viewing *****
//
// ShowRAExt();
//
// ****************************************

include<CommonStuffSAEmm.scad>

Overlap=0.05;
IDXtra=0.3;
$fn=$preview? 24:90;

	SM_Rod_d=0.0625*25.4;

	Dove_w=10;
	Dove_w2=6;
	Dove_h=3.5;
	Silde_L=14;
	RA_Pivot_Pin_d=3;

module ExtendedSlider(L=30){
	
	difference(){
		union(){
			Dovetail();
			
			translate([0,-L,0]) Dovetail();
			
			// torsion rod guides
			translate([0,Silde_L/4,0]){
				translate([0,2,Dove_h-Overlap]) cylinder(d=3,h=2);
				translate([0,-2,Dove_h-Overlap]) cylinder(d=3,h=2);
			} // translate
			
			// connector bar
			hull(){
				translate([0,-L,0]) cylinder(d=Dove_w2,h=2.2);
				cylinder(d=Dove_w2,h=2.2);
			} // hull
		} // union
		
		// throw rod
		translate([0,-L-Silde_L/4,0]){
		translate([0,0,-Overlap]) cylinder(d=SM_Rod_d+IDXtra*2,h=Dove_h);
		translate([0,0,1.3]) cylinder(d=4,h=Dove_h);
		} // translate
		
	} // difference
} // ExtendedSlider

// translate([-4,0,0]) ExtendedSlider(L=30);

module ShowRAExt(L=60){
	RASlider();
	translate([-8,-Silde_L/4-2,0.5+Dove_h+Overlap]) RAPivot();
	
	translate([-8,-14,0]) rotate([0,0,-90]) RAExtension(L=L);
	translate([-8-L,-14-4,-2.2]) rotate([0,0,-90]) ExtenderMount();

	translate([4,0,-2.2]) RAMountingBlock();
} // ShowRAExt

//ShowRAExt();

module Dovetail(W=Dove_w, W2=Dove_w2, L=Silde_L){
	hull(){
		translate([-W/2,-L/2,0]) cube([W,L,0.6]);
		translate([-W2/2,-L/2,Dove_h-0.01]) cube([Dove_w2,L,0.01]);
	} // hull
} // Dovetail

module RASlider(){
	
	difference(){
		union(){
			Dovetail();
			
			// torsion rod guides
			translate([0,Silde_L/4,0]){
				translate([0,2,Dove_h-Overlap]) cylinder(d=3,h=2);
				translate([0,-2,Dove_h-Overlap]) cylinder(d=3,h=2);
			}
            translate([0,-Silde_L/4,0])
				translate([0,-2,Dove_h-Overlap]) cylinder(d=RA_Pivot_Pin_d,h=3.0);
		} // union
		
	} // difference
} // RASlider

// RASlider();

module RAPivot(){
    RAP_h=2;
    
    PinSlop=1.4;
	OD_Add=4;
    
    difference(){
        union(){
            hull(){
                cylinder(d=RA_Pivot_Pin_d+OD_Add,h=RAP_h);
                translate([8+PinSlop,0,0]) cylinder(d=RA_Pivot_Pin_d+OD_Add,h=RAP_h);
            } // hull
            hull(){
                cylinder(d=RA_Pivot_Pin_d+OD_Add,h=RAP_h);
                translate([0,-8-PinSlop,0]) cylinder(d=RA_Pivot_Pin_d+OD_Add,h=RAP_h);
            } // hull
            
        }
        
        // pivot point
        translate([0,0,-Overlap]) cylinder(d=RA_Pivot_Pin_d+IDXtra*2, h=RAP_h+Overlap*2);
        
        translate([8,0,-Overlap]) hull(){
            translate([PinSlop,0,0]) cylinder(d=RA_Pivot_Pin_d+IDXtra*2, h=RAP_h+Overlap*2);
            translate([-1,0,0]) cylinder(d=RA_Pivot_Pin_d+IDXtra*2, h=RAP_h+Overlap*2);
        }
        translate([0,-8,-Overlap]) hull(){
            translate([0,1,0]) cylinder(d=RA_Pivot_Pin_d+IDXtra*2, h=RAP_h+Overlap*2);
            translate([0,-PinSlop,0]) cylinder(d=RA_Pivot_Pin_d+IDXtra*2, h=RAP_h+Overlap*2);
        }
    } // difference
    
} // RAPivot

//translate([-8,-Silde_L/4-2,0.5+Dove_h+Overlap]) RAPivot();

module RAExtension(L=30){
	
	difference(){
		union(){
			Dovetail();
			
			translate([0,-L,0]) Dovetail();
			
			// pivot end
				translate([0,0,Dove_h-Overlap]) cylinder(d=RA_Pivot_Pin_d,h=3.0);
				
			// connector bar
			hull(){
				translate([0,-L,0]) cylinder(d=Dove_w2,h=2.2);
				cylinder(d=Dove_w2,h=2.2);
			} // hull
           
		} // union
		
        // throw rod
		translate([0,-L-Silde_L/4,0]){
		translate([0,0,-Overlap]) cylinder(d=SM_Rod_d+IDXtra*2,h=Dove_h);
		translate([0,0,1.3]) cylinder(d=4,h=Dove_h);
		}
	} // difference
} // RAExtension

//translate([-8,-14,0]) rotate([0,0,-90]) RAExtension();
//translate([-8-30,-13.5-4,-2.2]) rotate([0,0,-90]) ExtenderMount();

module DovetailSlot(W=Dove_w, W2=Dove_w2, L=Silde_L){
	hull(){
		translate([-W/2-IDXtra,-L/2-Overlap,-IDXtra]) cube([W+IDXtra*2,L+Overlap*2,0.6+IDXtra]);
		translate([-W2/2-IDXtra,-L/2-Overlap,Dove_h-0.01]) cube([Dove_w2+IDXtra*2,L+Overlap*2,0.01]);
	} // hull
	translate([-W2/2-IDXtra,-L/2-Overlap,Dove_h-Overlap]) cube([Dove_w2+IDXtra*2,L+Overlap*2,4]);
} // DovetailSlot
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

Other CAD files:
MountingBox/STL/PivotBaseL.stl
MountingBox/AtlasTurnout STL/MountingBlock.stl
MountingBox/STL/PivotBaseLS.stl

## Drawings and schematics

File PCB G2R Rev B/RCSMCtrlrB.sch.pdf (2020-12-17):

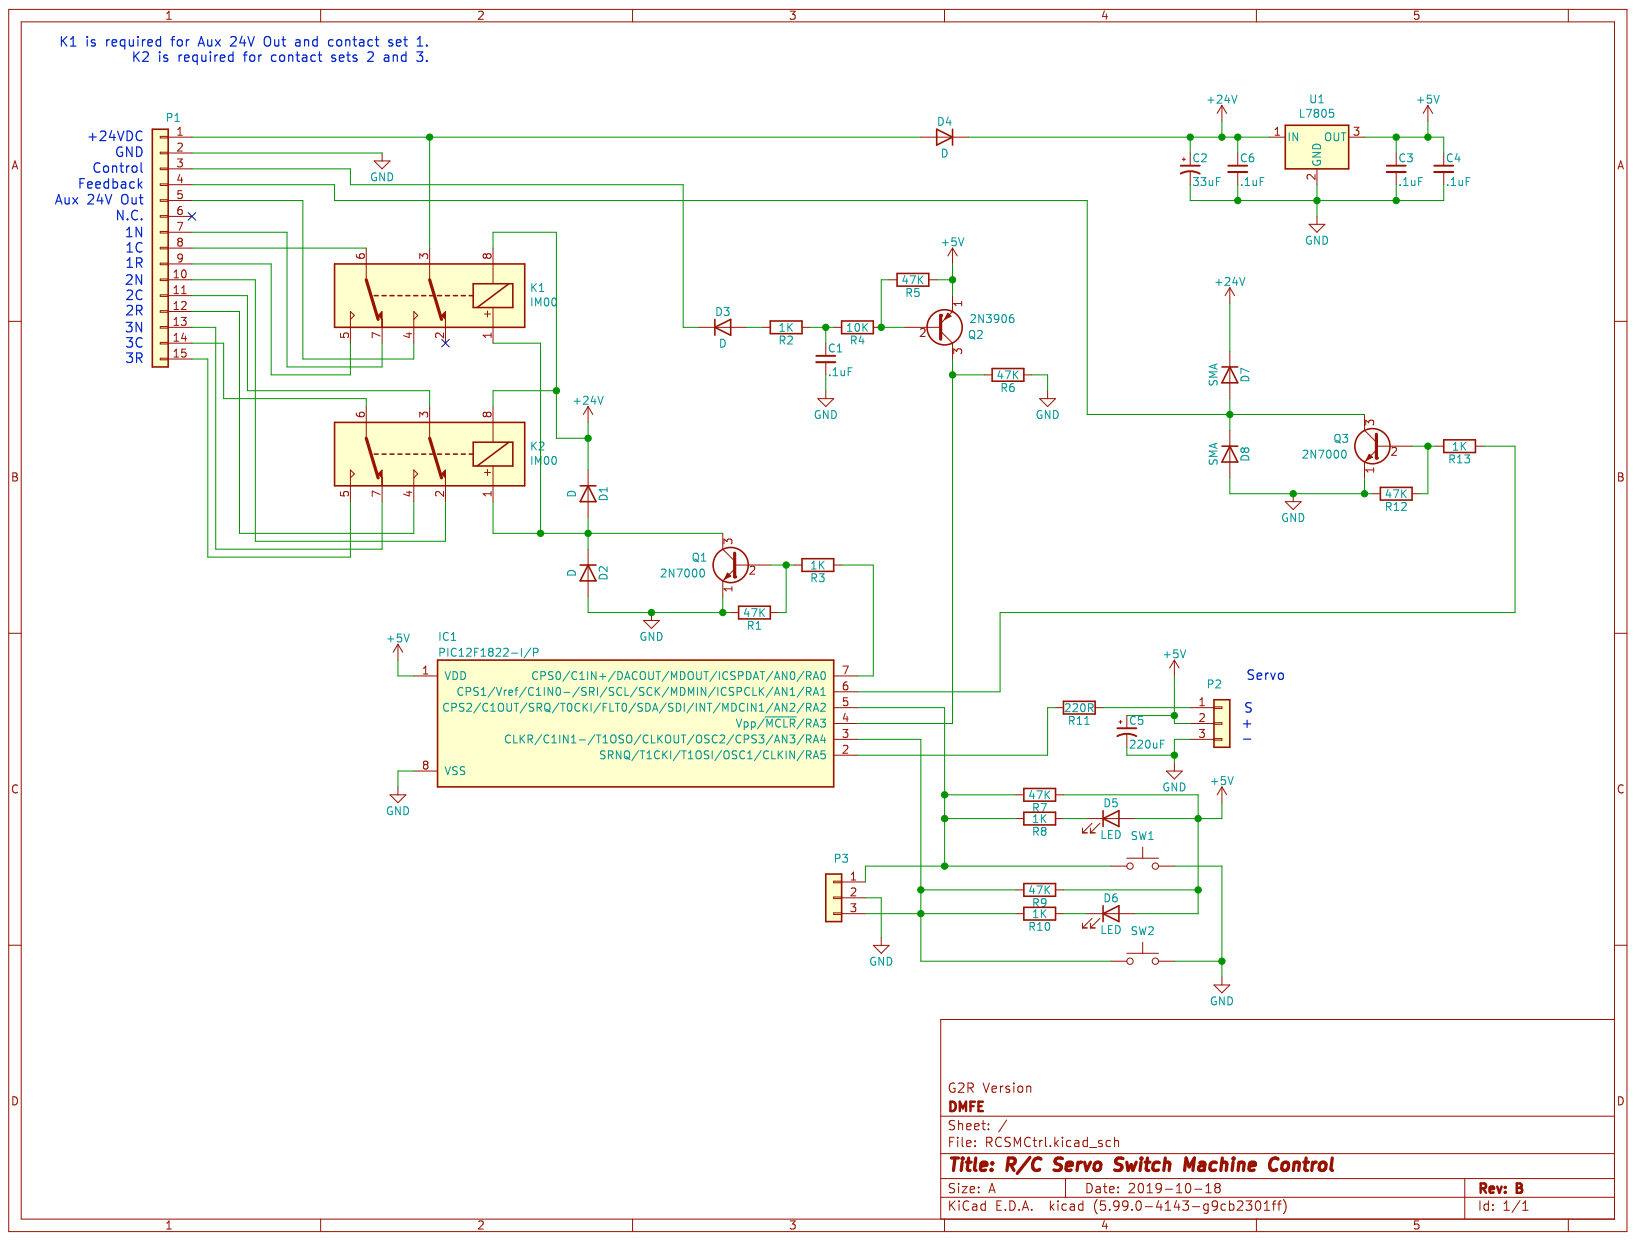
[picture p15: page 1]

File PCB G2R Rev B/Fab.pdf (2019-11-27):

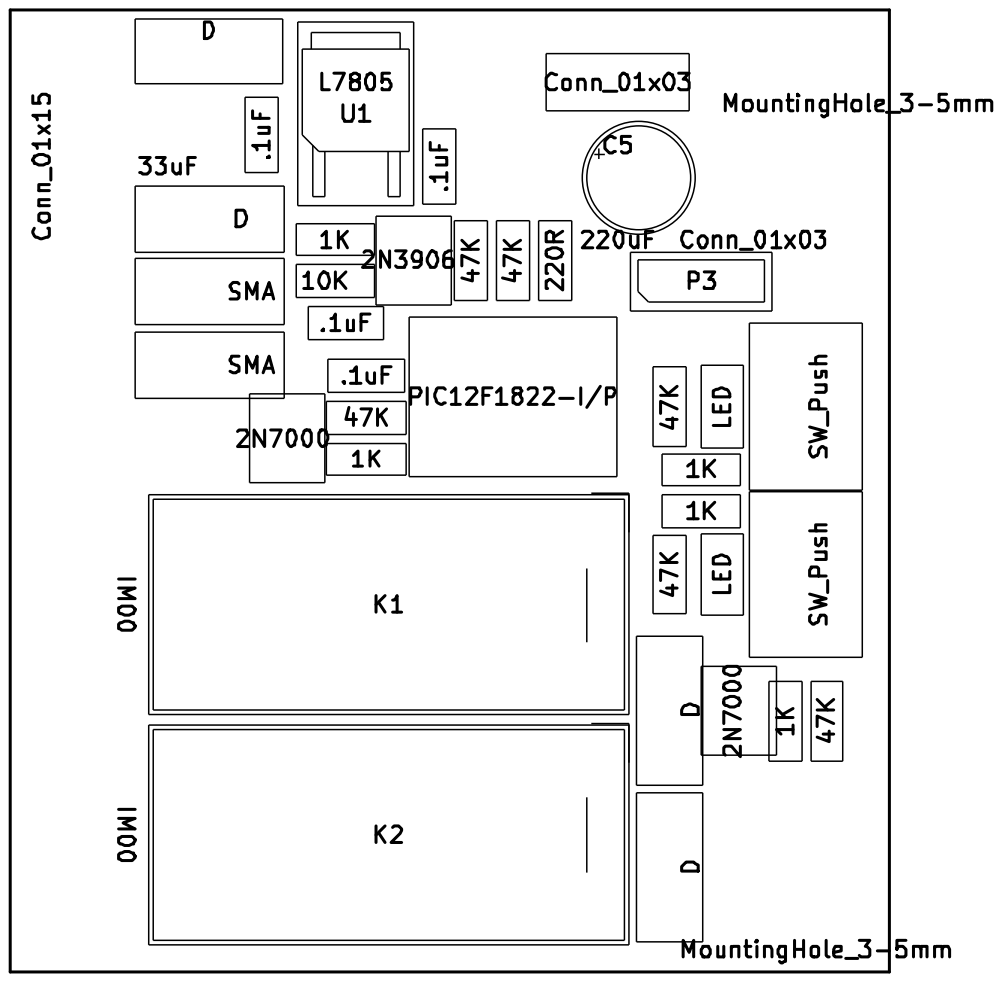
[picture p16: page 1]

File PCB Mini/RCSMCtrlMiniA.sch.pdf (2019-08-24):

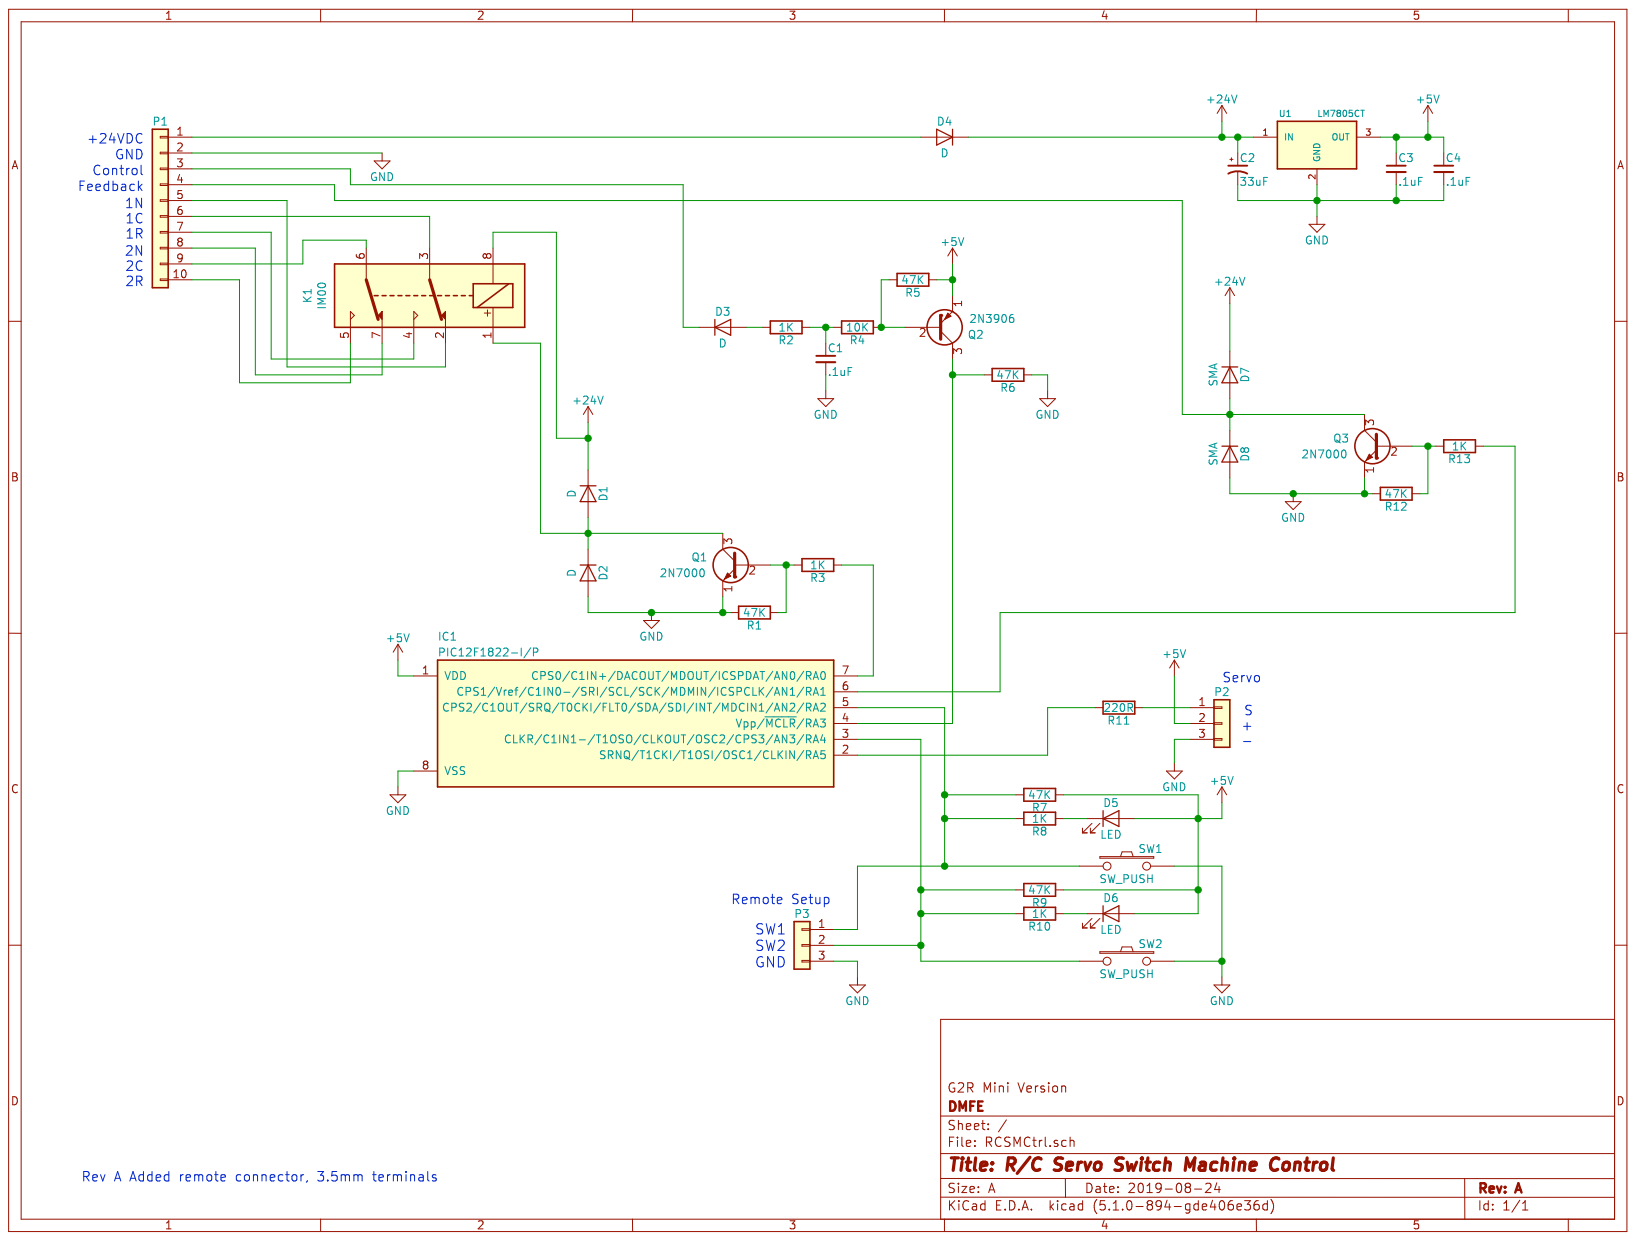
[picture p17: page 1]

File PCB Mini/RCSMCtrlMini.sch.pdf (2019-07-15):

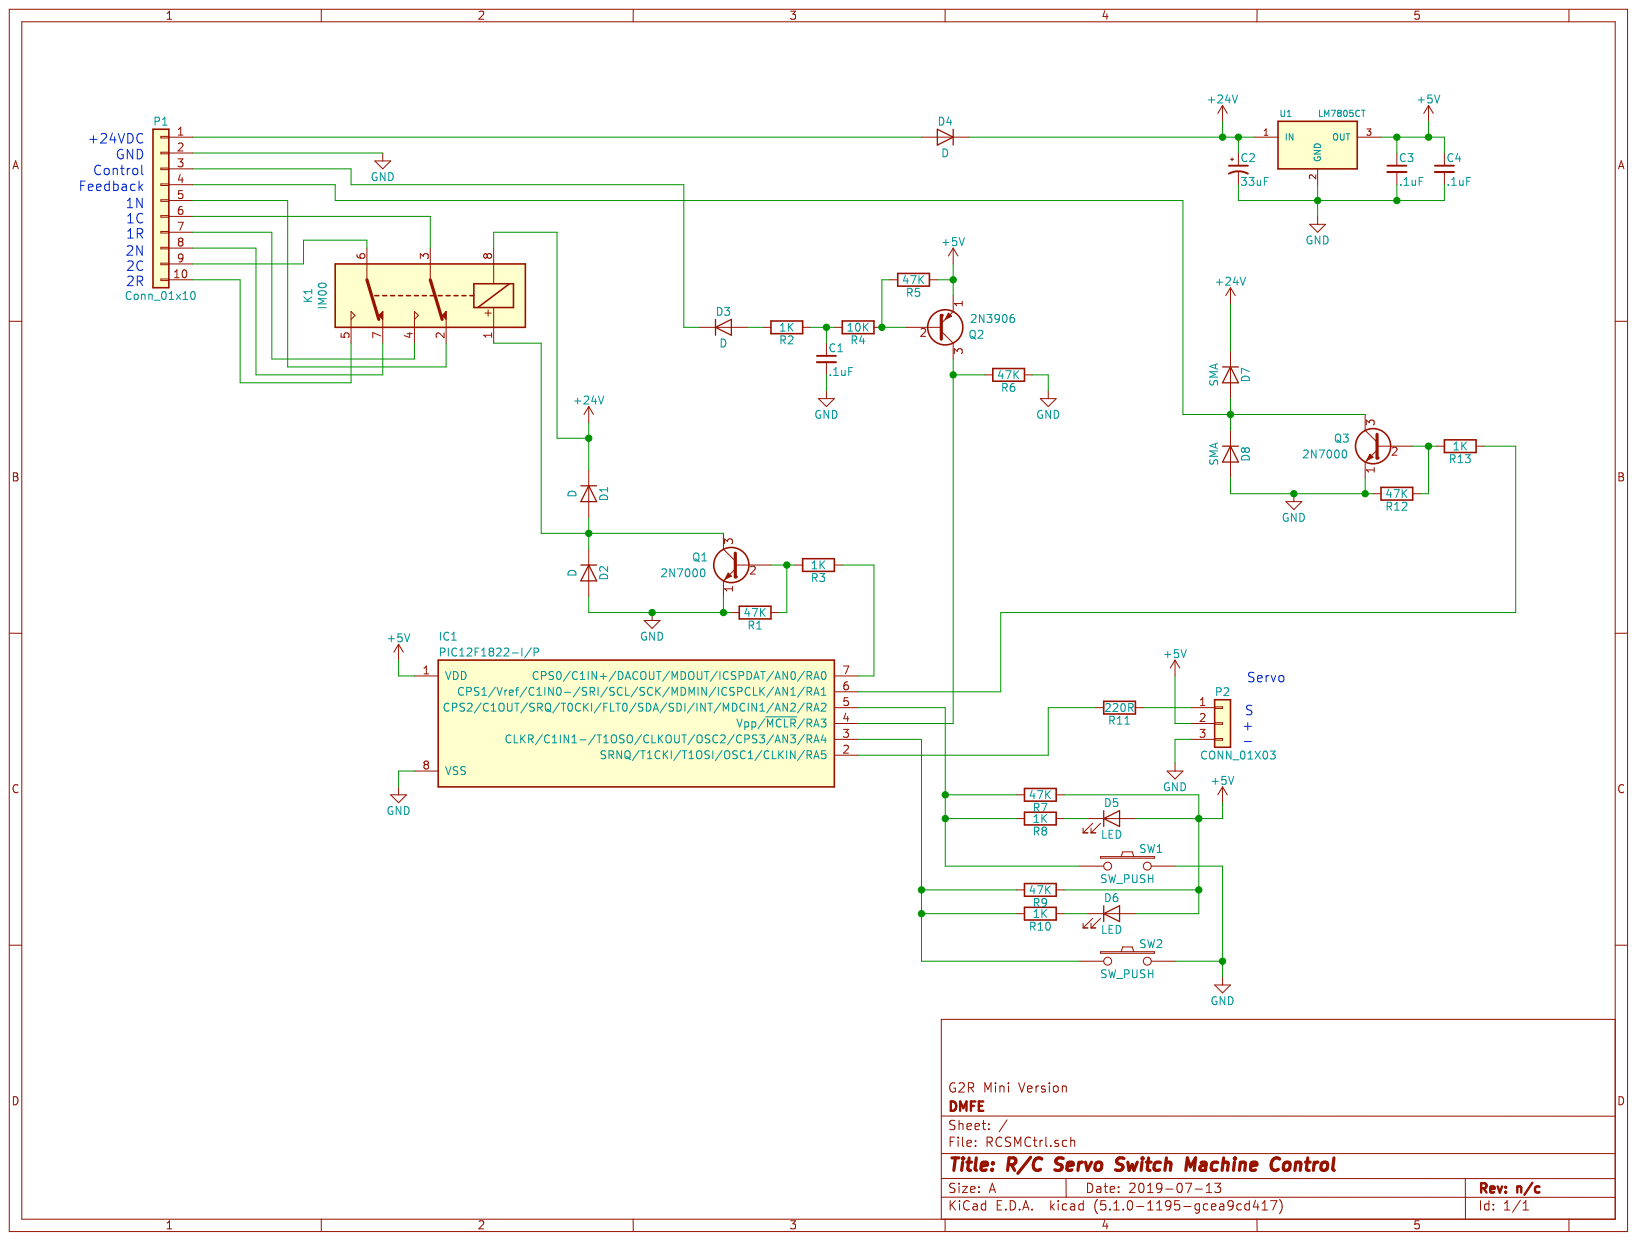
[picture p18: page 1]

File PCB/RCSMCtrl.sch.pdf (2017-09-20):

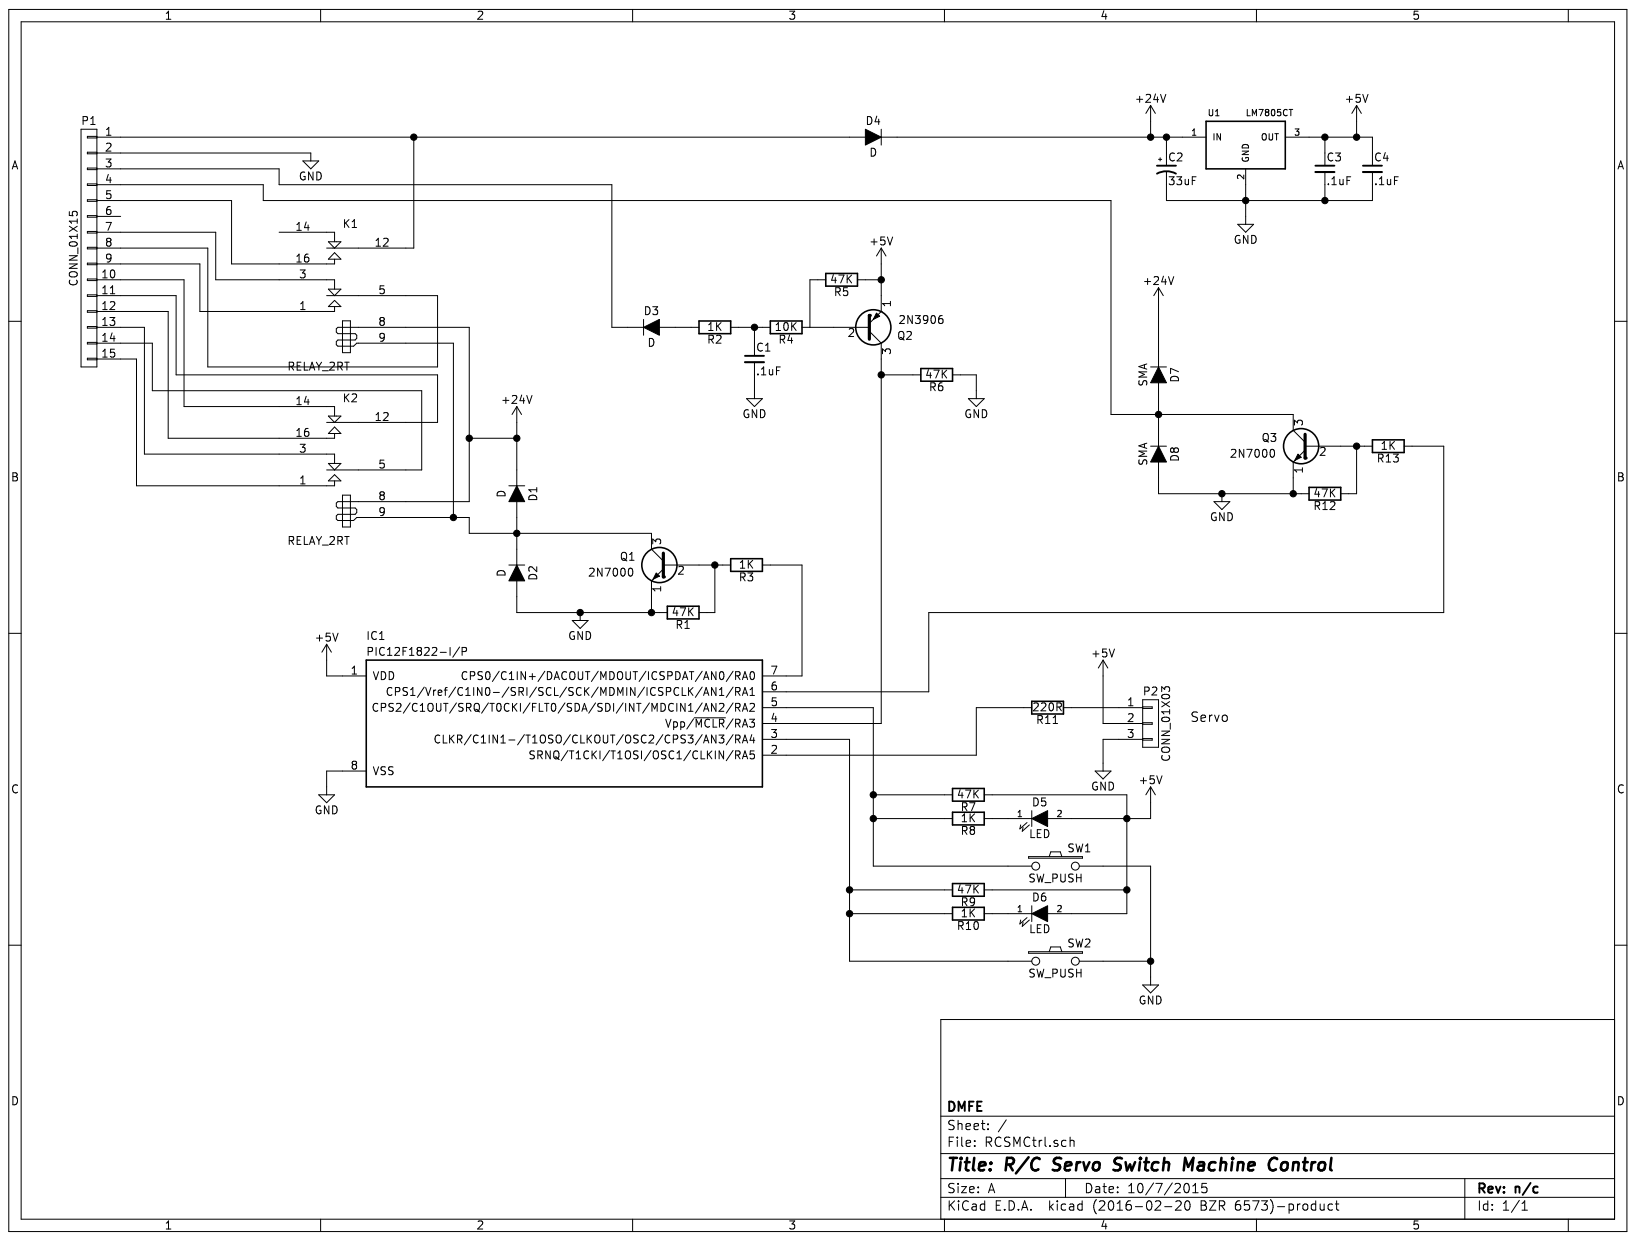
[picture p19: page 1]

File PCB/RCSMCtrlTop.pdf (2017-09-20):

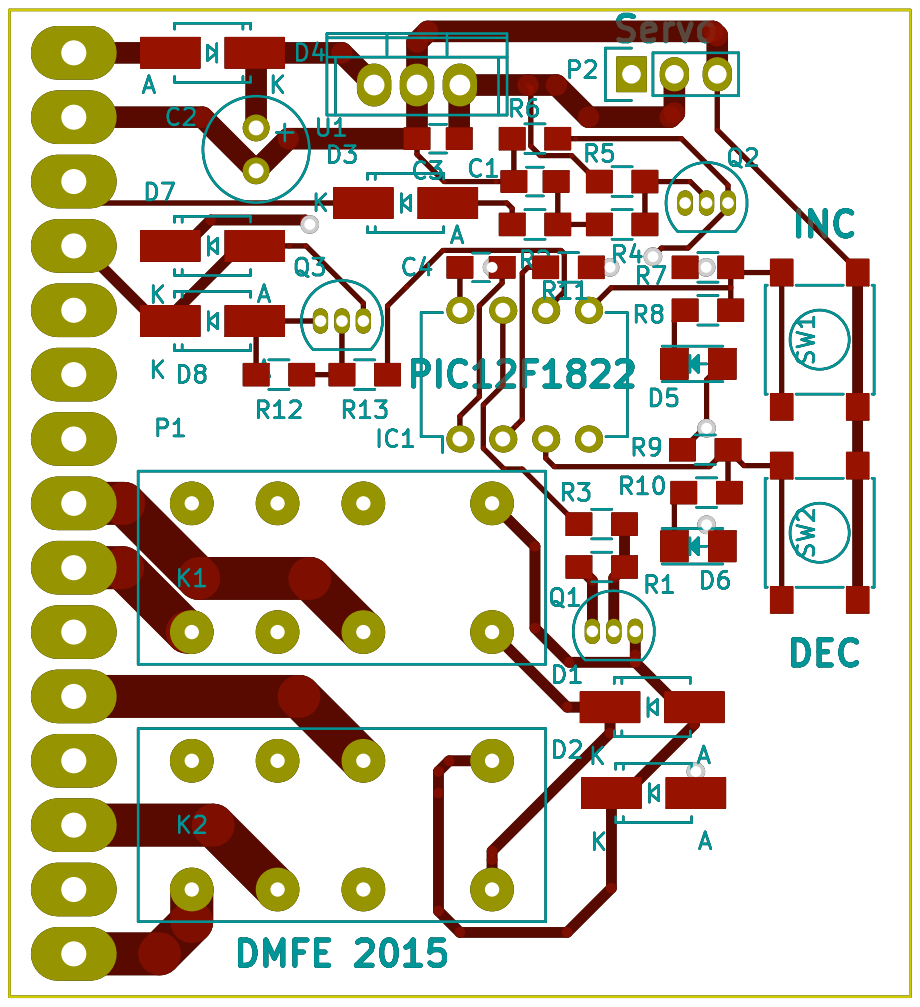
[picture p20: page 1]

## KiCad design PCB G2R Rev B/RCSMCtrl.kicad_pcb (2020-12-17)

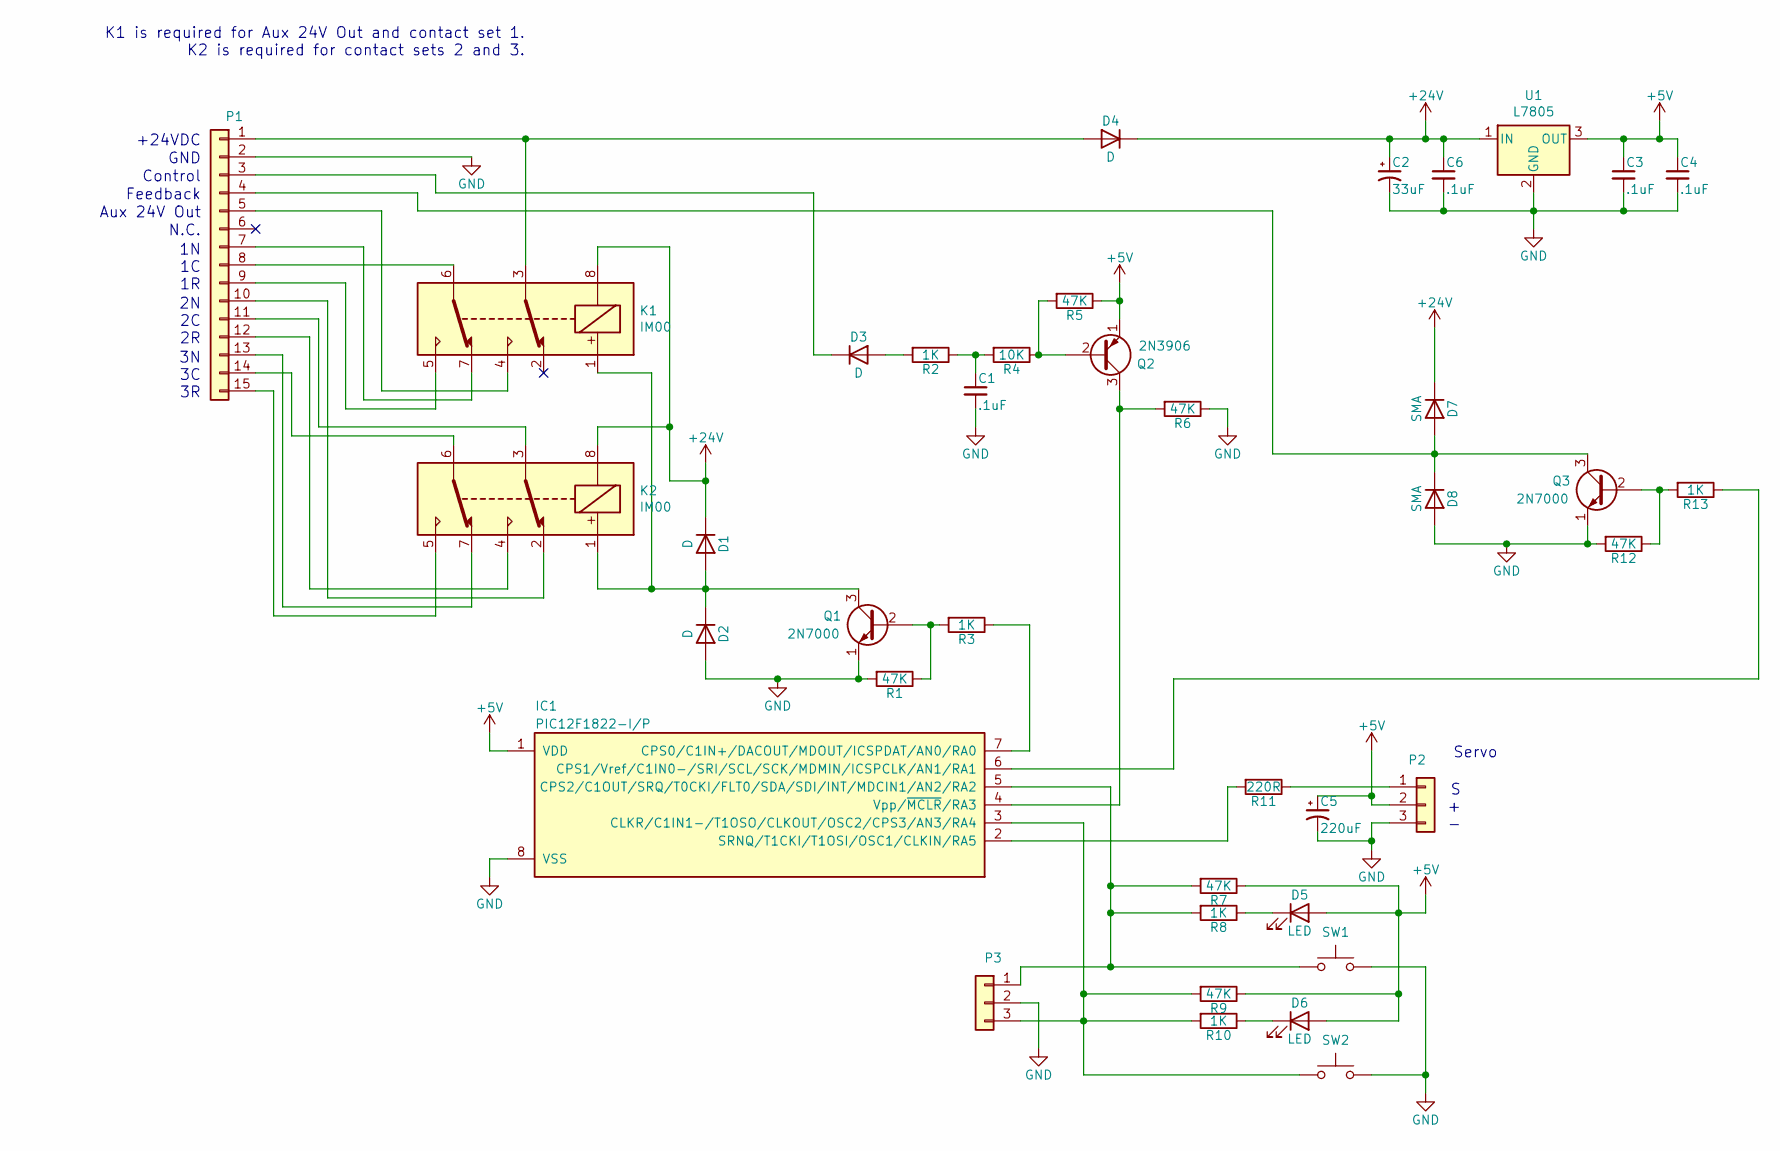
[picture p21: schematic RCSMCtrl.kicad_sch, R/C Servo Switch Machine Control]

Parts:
C1, C3, C4, C6: .1uF; C_0805_HandSoldering
C2: 33uF; Elko_vert_11.2x6.3mm_RM2.5_CopperClear
C5: 220uF; CP_Radial_D6.3mm_P2.50mm
D1, D2, D3, D4: D; Diode-SMA_Handsoldering
D5, D6: LED; LED-1206
D7, D8: SMA; Diode-SMA_Handsoldering
IC1: PIC12F1822-I/P; DIP-8_W7.62mm
K1, K2: IM00
P1: Conn_01x15
P2, P3: Conn_01x03; PinHeader_1x03_P2.54mm_Vertical
Q1, Q3: 2N7000; TO-92_Inline_Narrow_Oval
Q2: 2N3906; TO-92_Inline_Narrow_Oval
R1, R5, R6, R7, R9, R12: 47K; R_0805_HandSoldering
R2, R3, R8, R10, R13: 1K; R_0805_HandSoldering
R4: 10K; R_0805_HandSoldering
R11: 220R; R_0805_HandSoldering
SW1, SW2: SW_Push
U1: L7805

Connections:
+5V: C3.1, C4.1, C5.1, D5.2 (A), D6.2 (A), IC1.1 (VDD), P2.2, Q2.1 (E), R5.1, R7.1, R9.1, U1.3 (OUT)
+24V: C2.1, C6.1, D1.1 (K), D4.1 (K), D7.1 (K), K1.8, K2.8, U1.1 (IN)
GND: C1.2, C2.2, C3.2, C4.2, C5.2, C6.2, D2.2 (A), D8.2 (A), IC1.8 (VSS), P1.2, P2.3, P3.2, Q1.1 (E), Q3.1 (E), R1.2, R6.1, R12.2, SW1.2, SW2.2, U1.2 (GND)
unnamed: C1.1, R2.1, R4.2
unnamed: D1.2 (A), D2.1 (K), K1.1, K2.1, Q1.3 (C)
unnamed: D3.1 (K), P1.3
unnamed: D3.2 (A), R2.2
unnamed: D4.2 (A), K1.3, P1.1
unnamed: D5.1 (K), R8.1
unnamed: D6.1 (K), R10.1
unnamed: D7.2 (A), D8.1 (K), P1.4, Q3.3 (C)
unnamed: IC1.2 (SRNQ/T1CKI/T1OSI/OSC1/CLKIN/RA5), R11.2
unnamed: IC1.3 (CLKR/C1IN1-/T1OSO/CLKOUT/OSC2/CPS3/AN3/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), P3.3, R9.2, R10.2, SW2.1
unnamed: IC1.4 (Vpp/~MCLR~/RA3), Q2.3 (C), R6.2
unnamed: IC1.5 (CPS2/C1OUT/SRQ/T0CKI/FLT0/SDA/SDI/INT/M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), P3.1, R7.2, R8.2, SW1.1
unnamed: IC1.6 (CPS1/Vref/C1IN0-/SRI/SCL/SCK/MDMIN/ICSP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), R13.1
unnamed: IC1.7 (CPS0/C1IN+/DACOUT/MDOUT/ICSPDAT/AN0/RA0), R3.1
unnamed: K1.4, P1.5
unnamed: K1.5, P1.9
unnamed: K1.6, P1.8
unnamed: K1.7, P1.7
unnamed: K2.2, P1.10
unnamed: K2.3, P1.11
unnamed: K2.4, P1.12
unnamed: K2.5, P1.15
unnamed: K2.6, P1.14
unnamed: K2.7, P1.13
unnamed: P2.1, R11.1
unnamed: Q1.2 (B), R1.1, R3.2
unnamed: Q2.2 (B), R4.1, R5.2
unnamed: Q3.2 (B), R12.1, R13.2

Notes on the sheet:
+24VDC
GND
Control
Feedback
Aux 24V Out
N.C.
1N 1C 1R
2N 2C 2R
3N 3C 3R
K1 is required for Aux 24V Out and contact set 1. K2 is required for contact sets 2 and 3.
Servo
S + -

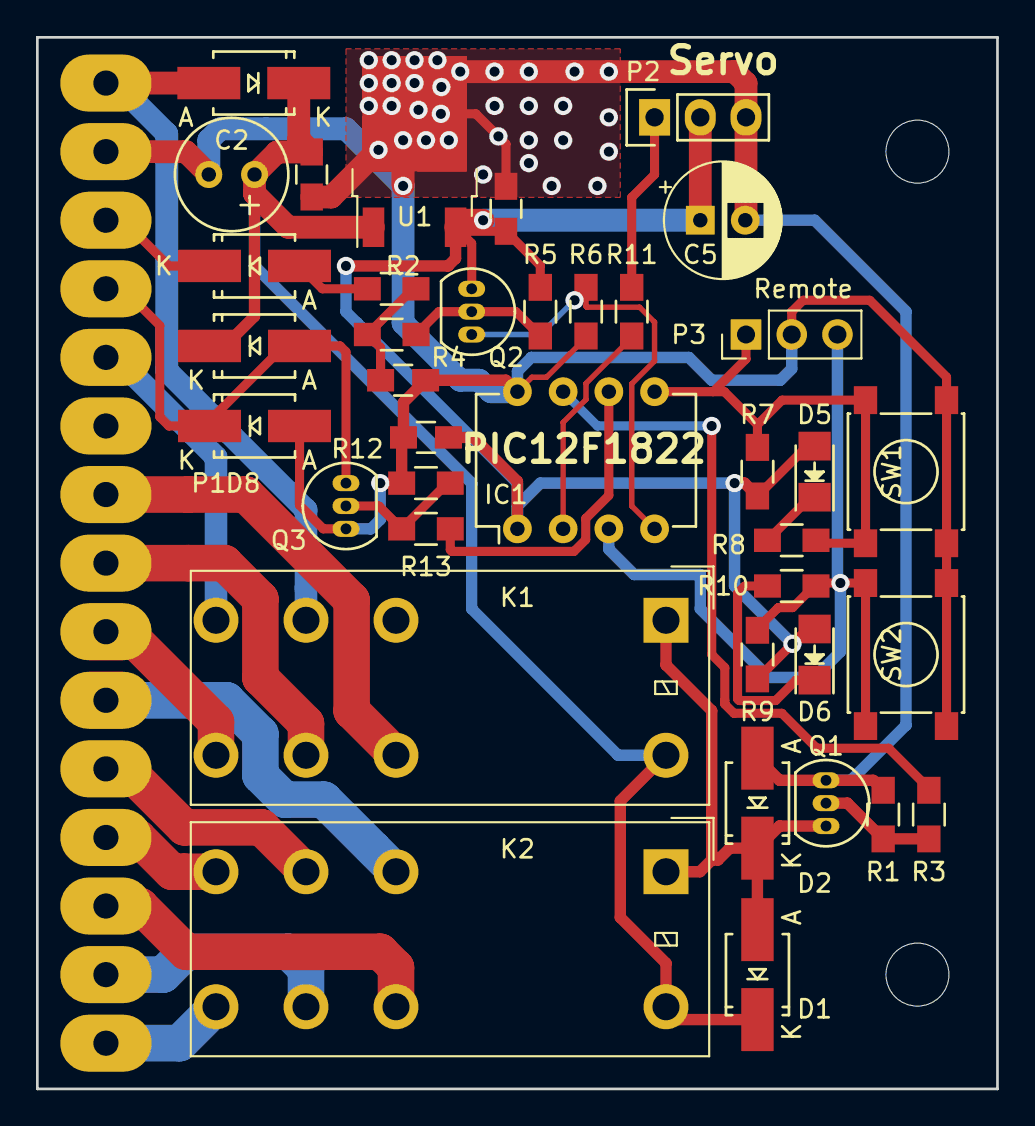
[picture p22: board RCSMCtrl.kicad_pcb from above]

Board: 2 copper layers, 53.3 x 58.4 mm, 41 parts (0 on the bottom side), 31 nets.

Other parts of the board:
H1, H2: MountingHole_3-5mm

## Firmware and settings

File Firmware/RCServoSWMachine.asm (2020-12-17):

;====================================================================================================
;
;   Filename:	RCServoSWMachine.asm
;   Date:	8/6/2019
;   File Version:	1.0b4
;
;    Author:	David M. Flynn
;    Company:	Oxford V.U.E., Inc.
;    E-Mail:	dflynn@oxfordvue.com
;    Web Site:	http://www.oxfordvue.com/
;
;====================================================================================================
;    RC Servo Switch Machine for PIC12F1822
;
;    History:
;
; 1.0b4   8/6/2019	FC1, Move to commanded position at power up. 1S servo powered time.
; 1.0b3   8/5/2019	Added move to center when both buttons are pressed.
; 1.0b2   7/20/2019	Delay at startup at mid point for 3 seconds, Slower motion for lower power.
; 	Stop senting pulses after in position for 0.5s.
; 1.0b1   9/18/2017    RC1, Looks like it works.
; 1.0d1   2/24/2016	Copied from RCServoTester1822
; 1.0a4   11/16/2015	Works as a servo tester w/ the PCB.  I2C is not tested/working.
; 1.0a3   1/15/2015	Added I2C slave
; 1.0a2   1/11/2015	Added Center button.
; 1.0a1   1/10/2015	First working tests.
; 1.0d1   9/4/2014	First Code.
;
;====================================================================================================
; Options
;====================================================================================================
; To Do's
;
;====================================================================================================
;====================================================================================================
; What happens next:
;
;   The system LED blinks once per second
;  Once at power-up:
;   Set position to the commanded position for 3 seconds.
;
;  Setup mode:
;   If SW1 is pressed Increment the set value for the control condition.
;   If SW2 is pressed Decrement the set value for the control condition.
;
;   If Control is High (active)
;      move to set point 1 turn on feedback, Aux and Relays
;   else if Control is Low (Normal, Inactive)
;      move to set point 2 turn off feedback, Aux and Relays
;
;   CCP1 outputs a 900uS to 2100uS (1800..4200 counts) pulse every 16,000uS
;
;   Resolution is 0.5uS
;
;  if kInPosShutdown is set servo will power down after 0.5s
;
;====================================================================================================
;
;  Pin 1 VDD (+5V)		+5V
;  Pin 2 RA5		CCP1
;  Pin 3 RA4		System LED Active Low/SW2 Dec switch Active Low
;  Pin 4 RA3/MCLR*/Vpp (Input only)	Command = Active High
;  Pin 5 RA2		LED 2 Active Low/SW1 Inc switch Active Low
;  Pin 6 RA1/ICSPCLK		Feedback Active High Output
;  Pin 7 RA0/ICSPDAT		Relay Control Active High Output
;  Pin 8 VSS (Ground)		Ground
;
;====================================================================================================
;
;
	list	p=12f1822,r=hex,w=1	; list directive to define processor
;
	nolist
	include	p12f1822.inc	; processor specific variable definitions
	list
;
	__CONFIG _CONFIG1,_FOSC_INTOSC & _WDTE_OFF & _MCLRE_OFF & _IESO_OFF
;
;
;
; INTOSC oscillator: I/O function on CLKIN pin
; WDT disabled
; PWRT disabled
; MCLR/VPP pin function is digital input
; Program memory code protection is disabled
; Data memory code protection is disabled
; Brown-out Reset enabled
; CLKOUT function is disabled. I/O or oscillator function on the CLKOUT pin
; Internal/External Switchover mode is disabled
; Fail-Safe Clock Monitor is enabled
;
	__CONFIG _CONFIG2,_WRT_OFF & _PLLEN_OFF & _LVP_OFF
;
; Write protection off
; 4x PLL disabled
; Stack Overflow or Underflow will cause a Reset
; Brown-out Reset Voltage (Vbor), low trip point selected.
; Low-voltage programming Disabled ( allow MCLR to be digital in )
;  *** must set apply Vdd before Vpp in ICD 3 settings ***
;
; '__CONFIG' directive is used to embed configuration data within .asm file.
; The lables following the directive are located in the respective .inc file.
; See respective data sheet for additional information on configuration word.
;
	constant	oldCode=0
	constant	useRS232=0
;
#Define	_C	STATUS,C
#Define	_Z	STATUS,Z
;
; 0.5uS res counter from 8MHz OSC
CCP1CON_Clr	EQU	b'00001001'	;Clear output on match
CCP1CON_Set	EQU	b'00001000'	;Set output on match
CCP1CON_Int	EQU	b'00001010'
;
kOffsetCtrValue	EQU	d'2047'
kMinPulseWidth	EQU	d'1800'	;900uS
kMidPulseWidth	EQU	d'3000'	;1500uS
kMaxPulseWidth	EQU	d'4200'	;2100uS
kDefaultPosition1	EQU	kMidPulseWidth+d'200'
kDefaultPosition2	EQU	kMidPulseWidth-d'200'
kServoDwellTime	EQU	d'40000'	;20mS
kInPosShutdown	EQU	b'00000010'	;b'00000010' enabled 0x00 disabled
;
;====================================================================================================
	nolist
	include	F1822_Macros.inc
	list
;
;    Port A bits
PortADDRBits	EQU	b'11011100'
#Define	RelayDrvrBit	LATA,0	;Active High Output
#Define	FeedbackBit	LATA,1	;Active High Output
#Define	LED2	LATA,2	;Output: 0=LED ON, Input: 0 = Switch Pressed
#Define	LED2TrisBit	TRISA,2
#Define	IncBtnBit	PORTA,2
#Define	CmdInputBit	PORTA,3
#Define	SystemLED	LATA,4	;Output: 0=LED ON, Input: 0 = Switch Pressed
#Define	SysLEDTrisBit	TRISA,4
#Define	DecBtnBit	PORTA,4
#Define	RA5_In	PORTA,5	;CCP1
;
PortAValue	EQU	b'00000000'
;
;====================================================================================================
;====================================================================================================
;
;Constants
All_In	EQU	0xFF
All_Out	EQU	0x00
;
LEDTIME	EQU	d'100'	;1.00 seconds
LEDErrorTime	EQU	d'10'
;
T1CON_Val	EQU	b'00000001'	;PreScale=1,Fosc/4,Timer ON
;T1CON_Val	EQU	b'00100001'	;PreScale=4,Fosc/4,Timer ON
OSCCON_Value	EQU	b'01110010'	;8MHz
;OSCCON_Value	EQU	b'11110000'	;32MHz
T2CON_Value	EQU	b'01001110'	;T2 On, /16 pre, /10 post
;T2CON_Value	EQU	b'01001111'	;T2 On, /64 pre, /10 post
PR2_Value	EQU	.125
;
;
CCP1CON_Value	EQU	0x00	;CCP1 off
;
DebounceTime	EQU	d'10'
;
;================================================================================================
;***** VARIABLE DEFINITIONS
; there are 128 bytes of ram, Bank0 0x20..0x7F, Bank1 0xA0..0xBF
; there are 256 bytes of EEPROM starting at 0x00 the EEPROM is not mapped into memory but
;  accessed through the EEADR and EEDATA registers
;================================================================================================
;  Bank0 Ram 020h-06Fh 80 Bytes
;
	cblock	0x20
;
	ISR_Temp		;scratch mem
	LED_Time
	LED2_Time
	LED_Ticks		;Timer tick count
	LED2_Ticks
;
;
	EEAddrTemp		;EEProm address to read or write
	EEDataTemp		;Data to be writen to EEProm
;
;
	Timer1Lo		;1st 16 bit timer
	Timer1Hi		; one second RX timeiout
	Timer2Lo		;2nd 16 bit timer
	Timer2Hi		;
	Timer3Lo		;3rd 16 bit timer
	Timer3Hi		;GP wait timer
	Timer4Lo		;4th 16 bit timer
	Timer4Hi		; debounce timer
;
	Dest:2
	CurPos:2
;
	Position1:2
	Position2:2
	SysFlags
;
	Debounce
;
	endc
;
#Define	PulseSent	SysFlags,0
#Define	InPosShutdown	SysFlags,1
#Define	InPosition	SysFlags,2
;
#Define	FirstRAMParam	Position1
#Define	LastRAMParam	SysFlags
;
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

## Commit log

2015-11-11 PCB is here, Firmware is next
    [RCSMCtrl-B_Cu.GBL, RCSMCtrl-B_Mask.GBS, RCSMCtrl-B_SilkS.GBO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]
2017-09-20 Here it is
    [Case1Rly.stl, Case2Rly.stl, CommonStuffSAE.scad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]
2019-07-14 2C Mini Version
    [RCSMCtrl-2019-07-13-21-21-59.sch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]
2019-07-15 Update 7/15
    [CaseBottom.stl, CaseTop1Rly.stl, CommonStuffSAE.scad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]
2019-07-16 servo mount
    [ServoArmMG996R.stl, ServoSMBlock.scad, ServoSMBlock.stl]
2019-07-21 Switching regulator
2019-08-06 Startup at correct position
    [RCServoSWMachine.asm]
2019-08-07 1.0b4 FC1
    [ServoSMBlock.scad, ServoSMBlock.stl, ServoSMBlockLeft.stl]
2019-08-09 A better block
    [ServoSMBlockG2RrA.stl, ServoSMBlockG2RrALeft.stl]
2019-08-24 mini rev A
    [RCSMCtrl-B_Cu.gbl, RCSMCtrl-B_Mask.gbs, RCSMCtrl-B_SilkS.gbo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]
2019-10-25 G2R Rev B
    [RCSMCtrl-2019-05-09-17-15-07.sch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]
2019-11-27 ready to print
    [RCSMCtrl.kicad_pcb]
2020-10-21 Atlas turnout driver (proto)
    [ServoSMBlock.scad, ServoSMBlockHX5010.stl, TS_Mount.stl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]
2020-10-21 Adjusted width
    [TurnoutSlider.scad]
2020-10-22 added lock and mirror versions
    [TurnoutSlider.scad]
2020-11-19 worked on RA mount
    [TurnoutSlider.scad]
2020-11-19 RA work...
    [TurnoutSlider.scad]
2020-11-21 V1.2.2 FC1
    [ExtendedSlider80.stl, ExtenderMount.stl, MBlock.stl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]
2020-11-21 RA mount #4 bolt
    [RAMountingBlock.stl, TurnoutSlider.scad]
2020-12-17 Fixed for MacroPIC
    [RCSMCtrl.kicad_pcb, RCSMCtrl.kicad_sch]
